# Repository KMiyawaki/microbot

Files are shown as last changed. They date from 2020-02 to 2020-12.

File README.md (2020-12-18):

# Microbot

Open source educational robot for Deep Leraning and ROS.

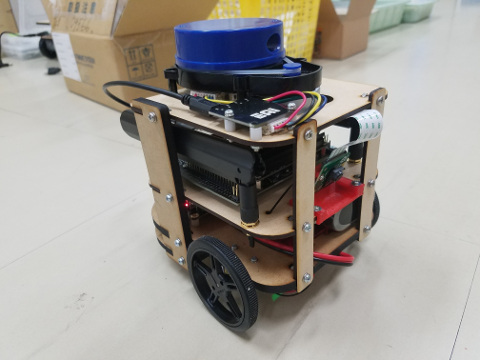
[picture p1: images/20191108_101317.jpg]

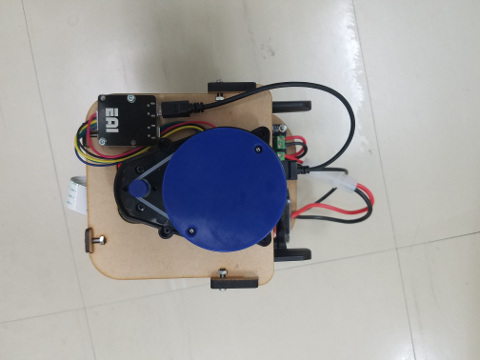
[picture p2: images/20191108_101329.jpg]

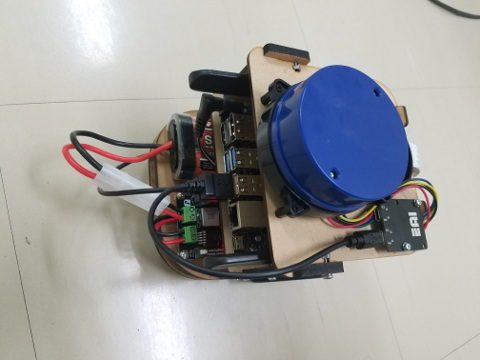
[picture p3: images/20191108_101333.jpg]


## SVG data for laser cutting

Use 5.5mm MDF board and 2.5mm MDF board

- [2.5mm](./Laser/Robot/2.5mm/All_2.5.svg)
- [5.5mm](./Laser/Robot/5.5mm/All_5.5.svg)

## Bills of materials

- [Microbot_BOM.pdf](./Microbot_BOM.pdf)

## Documents

- [Micorbot Manual](https://github.com/KMiyawaki/lectures/blob/master/ros/robots/jetson_microbot_boot_shutdown.md)
- [Jetson NANO カスタムイメージの作成](jetson_sdk.md)
- [JetCard のインストール](install_jetcard.md)
- [その他のソフトのインストール](setup_details.md)

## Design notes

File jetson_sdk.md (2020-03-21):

# NVIDIA SDK manager & docker

## Docker をインストール

- https://qiita.com/myyasuda/items/cb8e076f4dba5c41afbc
- `docker`グループに参加し、再起動する

```shell
$ sudo usermod -aG docker `whoami`
$ sudo reboot
```

- `docker ps`で以下のような出力があれば OK。

```shell
$ docker ps
CONTAINER ID        IMAGE               COMMAND             CREATED             STATUS              PORTS               NAMES
```

## 事前に大容量の領域を確保する

- ツインドライブ構成 PC の HDD に Linux 領域を作成するなど。
- `/etc/fstab`に設定を書き、マウントしておく。ここでは`/hdd`にその領域をマウントしたとして進める。
- Docker イメージの置き場所を大容量領域に変える。
  - https://qiita.com/elm200/items/43497f76cbdd19c47d8b

```shell
$ sudo systemctl stop docker.service
$ sudo mv /var/lib/docker /hdd
$ cd /etc/docker
$ sudo emacs daemon.json -nw
```

- `daemon.json`の内容は次の通り

```json
{
  "data-root": "/hdd/docker"
}
```

## Docker イメージを作成する

- `Dockerfile`をクローン

```shell
$ cd /hdd
$ git clone https://github.com/atinfinity/sdk_manager_docker.git
```

- https://developer.nvidia.com/nvidia-sdk-manager から`NVIDIA SDK Manager`バイナリをダウンロード

  - NVIDIA Developper のアカウント必要。
  - `sdkmanager_1.0.1-5538_amd64.deb` (2020/03/21 時点) このファイルを上記`sdk_manager_docker`に移動させておく。

- Docker イメージのビルド

```shell
$ cd sdk_manager_docker
$ docker build --build-arg SDK_MANAGER_VERSION=1.0.1-5538 -t jetpack .
```

- イメージの確認
  - `docker images`コマンド

```shell
$ docker images
REPOSITORY          TAG                 IMAGE ID            CREATED             SIZE
jetpack             latest              67e7931be86e        5 minutes ago       811MB
ubuntu              18.04               ccc6e87d482b        13 days ago         64.2MB
```

- Docker コンテナから X サーバーへの通信を許可する。
  - https://unskilled.site/docker%E3%82%B3%E3%83%B3%E3%83%86%E3%83%8A%E3%81%AE%E4%B8%AD%E3%81%A7gui%E3%82%A2%E3%83%97%E3%83%AA%E3%82%B1%E3%83%BC%E3%82%B7%E3%83%A7%E3%83%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
  - ホストマシン起動時に毎回必要。

```shell
$ xhost local:
non-network local connections being added to access control list
```

- ホストマシンのディレクトリを永続化領域として指定する。
  - `sdk_manager_docker/launch_container.sh`に追記してコンテナで作成したデータが消えないようにする。

```text
docker run --privileged --rm -it \
           --volume=$XSOCK:$XSOCK:rw \
           --volume=$XAUTH:$XAUTH:rw \
           --volume=/dev:/dev:rw \
           --volume=/hdd:/hdd:rw \ # 追記
```

## SDK Manager の起動

- ホストマシンのディスク容量をチェック

```shell
$ df -alh
/dev/nvme0n1p5   94G   21G   69G  24% /     # SSD 領域。ここは使わないようになっているはず。
/dev/sda2       393G  1.1G  372G   1% /hdd  # Dockerイメージを作成したHDD領域。
```

- コンテナ起動

```shell
$ cd /hdd/sdk_manager_docker
$ ./launch_container.sh
```

- コンテナ側で SDK Manager 起動

```shell
$ sdkmanager
```

- Step 1
  - Host Machine のチェックを外す。
  - Target Hardware を Jetson NANO (Developper kit version)にする。
  - Target Operating System を JetPack 4.2.2 (rev. 1) にする。
    - Jetcard のブランチ名に合わせているだけ。

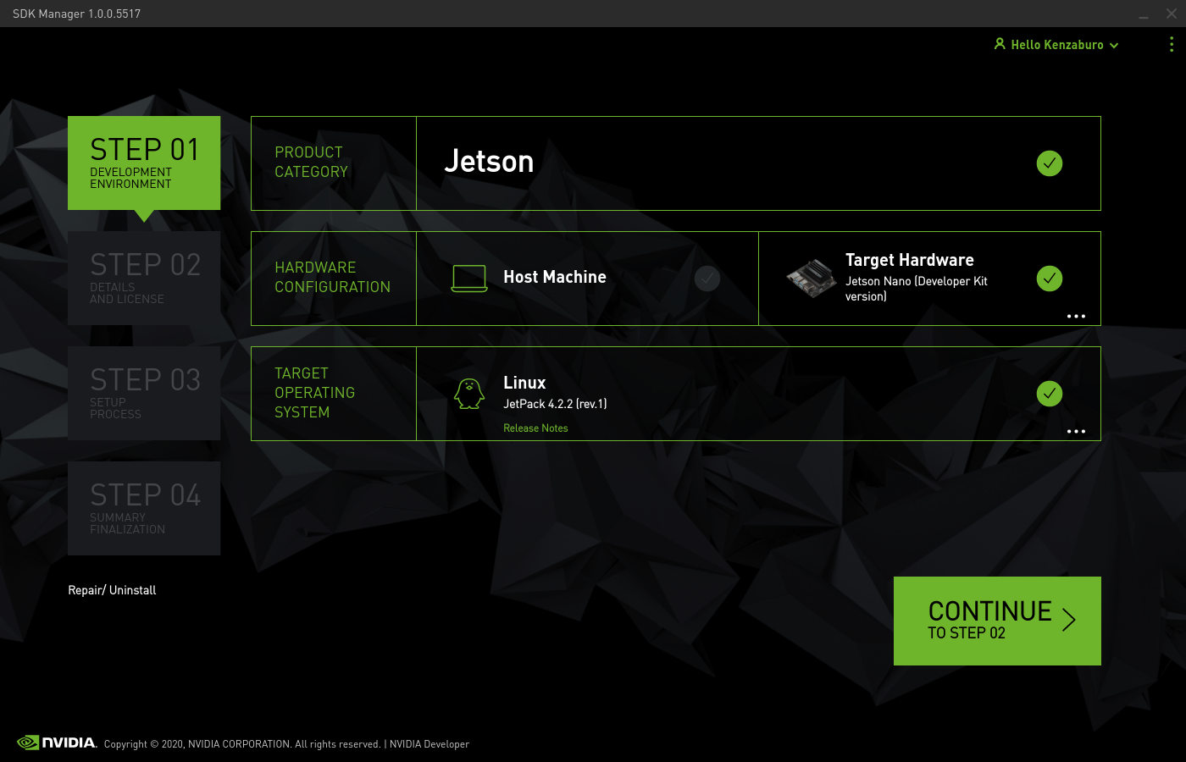
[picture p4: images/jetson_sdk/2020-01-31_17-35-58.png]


- Step 2
  - Jetson SDK Components のチェックを外す。

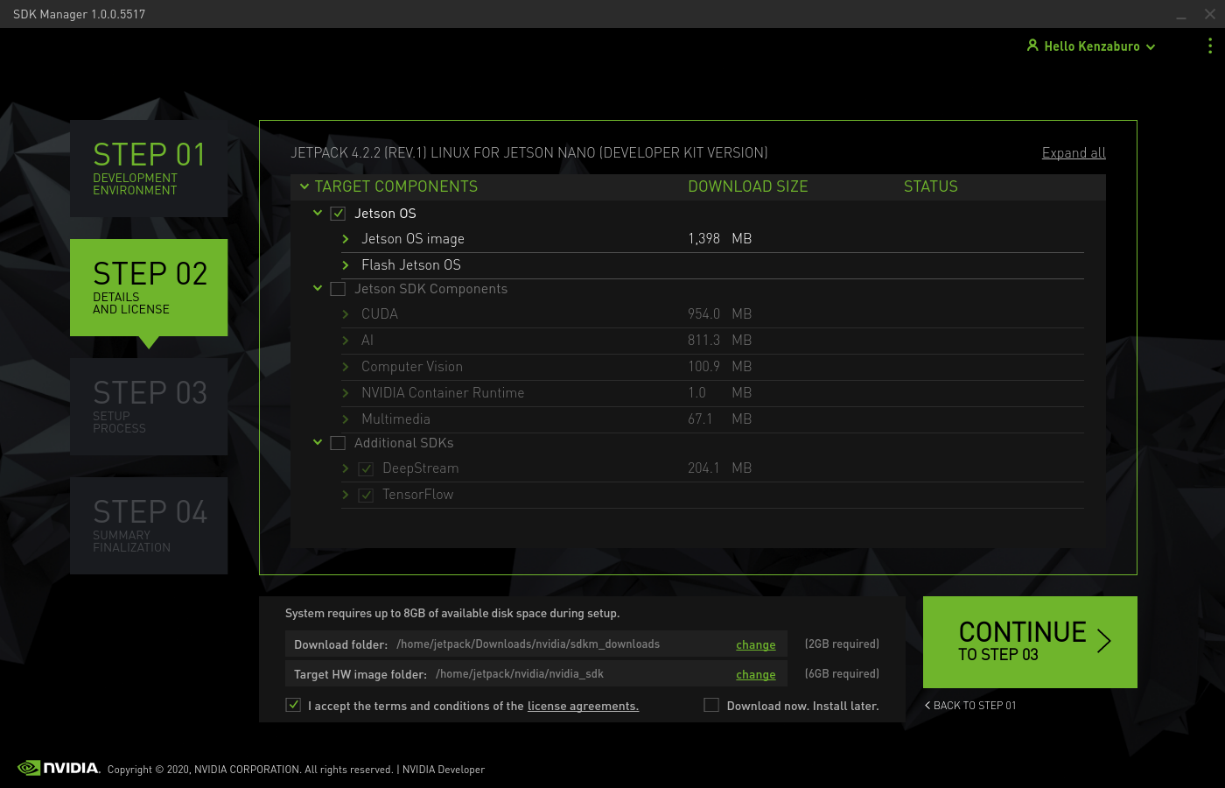
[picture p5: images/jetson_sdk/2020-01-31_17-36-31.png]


- Step 3
  - ダウンロードが始まる。

## イメージ作成に必要なファイルを抽出する

- Docker コンテナで SDK Manager によりダウンロードしたファイル群から必要なものをコピーする。

```shell
$ cd /hdd
$ mkdir nano_sd_image
$ cd nano_sd_image/
$ sudo cp -ra ~/nvidia/nvidia_sdk/JetPack_4.2.2_Linux_GA_P3448/Linux_for_Tegra/. ./
$ cp rootfs/etc/systemd/nvresizefs.sh ./
$ sudo cp rootfs/etc/systemd/system/nvresizefs.service ./
$ sudo rm -rf /hdd/nano_sd_image/rootfs/*
```

## コピーもとの Jetson NANO SD カードからデータを抽出する

- Docker 側で作成した`nano_sd_image`ディレクトリを**ホスト側**で確認する。

```shell
$ cd /hdd
$ ls
docker  nano_sd_image  sdk_manager_docker
$ cd /hdd/nano_sd_image
$ df -BG|grep media
/dev/sdb1           118G   24G       89G  22% /media/<ユーザ名>/<デバイス名>
$ sudo cp -ra /media/<ユーザ名>/<デバイス名>/. rootfs/
```

## コンテナ側でイメージを作成する

- 自動拡張スクリプトの補充

```shell
$ cd /hdd/nano_sd_image
$ sudo cp nvresizefs.sh rootfs/etc/systemd/
$ sudo cp nvresizefs.service rootfs/etc/systemd/system/
$ sudo ln -s rootfs/etc/systemd/system/nvresizefs.service rootfs/etc/systemd/system/multi-user.target.wants/nvresizefs.service
```

- sgdisk コマンドのために gdisk をインストール

```shell
$ sudo apt-get install -y gdisk
```

- イメージの作成（10 分程度）
  - `df -BG|grep media`で得られた使用済み容量より大きい値を`./create-jetson-nano-sd-card-image.sh`の引数に指定する。

```shell
$ cd /hdd/nano_sd_image
$ sudo ./create-jetson-nano-sd-card-image.sh -o backup.img -s 25G -r 200 # 25G はSDカードの使用済み容量より大きい値を設定する。
********************************************
     Jetson-Nano SD Image Creation Tool
********************************************
create-jetson-nano-sd-card-image.sh - creating backup.img of 25G...
0+0 records in
0+0 records out
0 bytes copied, 4.3765e-05 s, 0.0 kB/s
create-jetson-nano-sd-card-image.sh - creating signed images
・・・
Allocating group tables: done
Writing inode tables: done
Creating journal (32768 blocks): done
Writing superblocks and filesystem accounting information: done

********************************************
   Jetson-Nano SD Image Creation Complete
********************************************
```

- 完成したイメージを[Etcher](https://www.balena.io/etcher/)などで別の SD に焼く。

## 補足

- Docker イメージの削除
  - https://qiita.com/tifa2chan/items/e9aa408244687a63a0ae

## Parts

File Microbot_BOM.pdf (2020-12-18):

Microbot BOM | 2020/12/18
部品番号 | サムネイル | 部品構成 | 見積費用 | 数量 | ベンダー | Web リンク | 材料 | 説明
RoboClaw 2x7A | | 購入 | ¥8,657 | 1 BASIC MICRO | | https://www.basicmicro.com/Roboclaw-2x7A-Motor- Controller_p_55.html
DC-DC Power Module 25W | | 購入 | ¥1,200 | 1 DFRobot | | https://www.dfrobot.com/product-752.html
ジーフォース GE021 SMASH NiMH7.2V3800mAh [ラジ コン用バッテリー] | | 購入 | ¥3,800 | 1 GForce | | http://www.gforce-hobby.jp/products/GE020.html
(+)ナベ頭小ねじ(ステンレス) M2.6x10 | | スタンダード | ¥4 | 3 Monotaro | | https://www.monotaro.com/p/0550/7065/
(+)ナベ頭小ねじ(ステンレス) M2.6x5 | | スタンダード | ¥4 | 12 Monotaro | | https://www.monotaro.com/p/0550/7031/
(+)ナベ頭小ねじ(ステンレス) M2.6x8 | | スタンダード | ¥4 | 4 Monotaro | | https://www.monotaro.com/p/0550/7056/
(+)ナベ頭小ねじ(ステンレス) M2x8 | | スタンダード | ¥4 | 8 Monotaro | | https://www.monotaro.com/p/0550/6934/
(+)ナベ頭小ねじ(ステンレス) M3×12 | | スタンダード | ¥4 | 18 Monotaro | | https://www.monotaro.com/p/0550/7205/
スプリングワッシャー(鉄/ユニクローム) M2 | | スタンダード | ¥1 | 8 Monotaro | | https://www.monotaro.com/p/0552/9867/
スプリングワッシャー(鉄/ユニクローム) M2.6 | | スタンダード | ¥1 | 23 Monotaro | | https://www.monotaro.com/p/0552/9973/
スプリングワッシャー(鉄/ユニクローム) M3 | | スタンダード | ¥0 | 18 Monotaro | | https://www.monotaro.com/p/0552/9876/
六角ナット1種(鉄/ユニクローム) パック入 り M2 | | スタンダード | ¥2 | 8 Monotaro | | https://www.monotaro.com/p/2344/2502/

1／3

部品番号 | サムネイル | 部品構成 | 見積費用 | 数量 | ベンダー | Web リンク | 材料 | 説明
六角ナット1種(鉄/ユニクローム) パック入 り M2.6 | | スタンダード | ¥2 | 15 Monotaro | | https://www.monotaro.com/p/2344/2536/
六角ナット1種(鉄/ユニクローム) パック入 り M3 | | スタンダード | ¥1 | 18 Monotaro | | https://www.monotaro.com/p/0552/9167/
camera_mount | | スタンダード | | 1 nVidia | | https://github.com/NVIDIA-AI- IOT/jetbot/blob/master/assets/camera_mount.stl | | 3Dプリント
Jetson NANO Developper Kit | | 購入 | ¥11,400 | 1 NVidia | | https://ryoyo-gpu.jp/products/jetson/nano2/
MicrobotBottomPlate | | スタンダード | | 1 OIT | | | MDF 中密度繊維ボード | 2.5mm
MicrobotCasterPlate | | スタンダード | | 1 OIT | | | MDF 中密度繊維ボード | 5.5mm
MicrobotCasterSpacer | | スタンダード | | 1 OIT | | | MDF 中密度繊維ボード | 5.5mm
MicrobotFrontPlate | | スタンダード | | 2 OIT | | | MDF 中密度繊維ボード | 2.5mm
MicrobotMiddlePlate | | スタンダード | | 1 OIT | | | MDF 中密度繊維ボード | 2.5mm
MicrobotSidePlate | | スタンダード | | 2 OIT | | | MDF 中密度繊維ボード | 5.5mm
MicrobotTopPlate | | スタンダード | | 1 OIT | | | MDF 中密度繊維ボード | 2.5mm
100:1 金属マイクロギヤードモータ HPCB 12V 両軸仕様 | | 購入 | ¥2,133 | 2 Pololu | | https://store.shopping.yahoo.co.jp/suzakulab/pololu- 3052.html

2／3

部品番号 | サムネイル | 部品構成 | 見積費用 | 数量 | ベンダー | Web リンク | 材料 | 説明
ホイール 60×8mm ブラック 2個入り | | 購入 | ¥479 | 1 Pololu | | https://store.shopping.yahoo.co.jp/suzakulab/Pololu- 1420.html
金属マイクロギヤードモータ 拡張ブラ ケット 2個入り | | 購入 | ¥562 | 1 Pololu | | https://store.shopping.yahoo.co.jp/suzakulab/pololu- 1089.html
ＲａｓｐｂｅｒｒｙＰｉカメラモジュール Ｖ２ | | 購入 | ¥4,300 | 1 RSコンポーネンツ株式会社 | | https://jp.rs-online.com/web/p/video- modules/9132664/
YDLidar X4 | | 購入 | ¥12,100 | 1 Shenzhen EAI Technology Co., Ltd | | https://www.switch-science.com/catalog/5412/
面打ボールキャスター BM-15 | | 購入 | ¥560 | 1 スガツネ工業 | | http://search.sugatsune.co.jp/product/g/gBM/
SJA-2606 | | スタンダード | ¥18 | 4 テイシン | | https://www.monotaro.com/p/0990/7162/ | | 六角両雌ねじスペーサー
SJB-2606 | | 購入 | ¥30 | 8 テイシン | | https://www.monotaro.com/p/0990/8422/
LP-02-1 【タミヤコネクタ】6.2mmピッチ 中継用L コネクタ プラグハウジング | | | | | 日本圧着端子製造 (JST) | https://www.sengoku.co.jp/mod/sgk_cart/detail.php?c ode=EEHD-4KC7

リード線

Pololu 金属マイクロギヤードモータ用磁気 エンコーダキット 12CPR 2.7V-18V (HPCB対応) 2個入り | | | 1108 | 1 | | https://store.shopping.yahoo.co.jp/suzakulab/Pololu- 3081.html | | 半田付けが非常に難しいので、販売元に有料委託する か、後継機種 （https://store.shopping.yahoo.co.jp/suzakulab/Pololu-4760.html）の利用を推奨（動作未確認）。

3／3

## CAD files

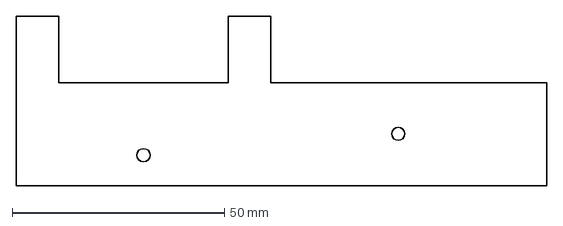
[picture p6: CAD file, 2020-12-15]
Laser/Base/Side.dxf
125.0 x 40.0 mm

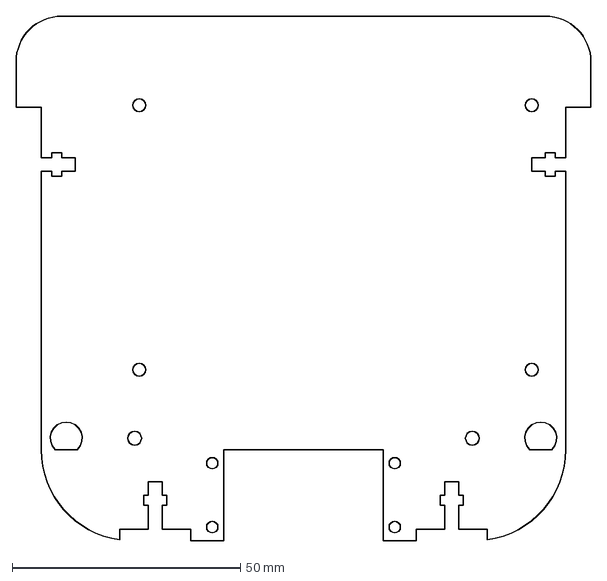
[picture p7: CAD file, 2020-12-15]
Laser/Robot/2.5mm/Middle.dxf
126.0 x 115.0 mm

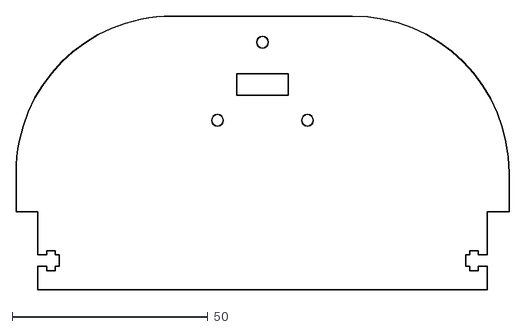
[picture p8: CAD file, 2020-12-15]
Laser/Robot/5.5mm/CasterBase.dxf
126.0 x 70.0

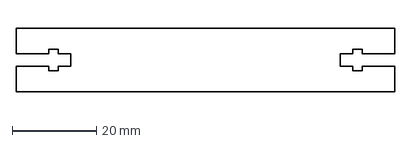
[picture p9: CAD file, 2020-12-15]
Laser/Base/BasePlate.dxf
90.0 x 15.0 mm

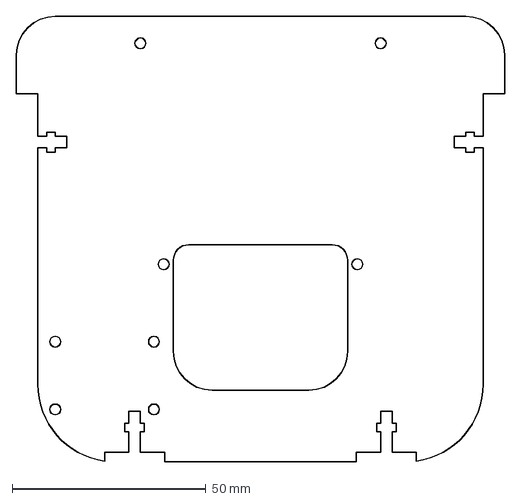
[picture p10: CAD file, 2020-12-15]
Laser/Robot/2.5mm/Top.dxf
126.0 x 115.0 mm

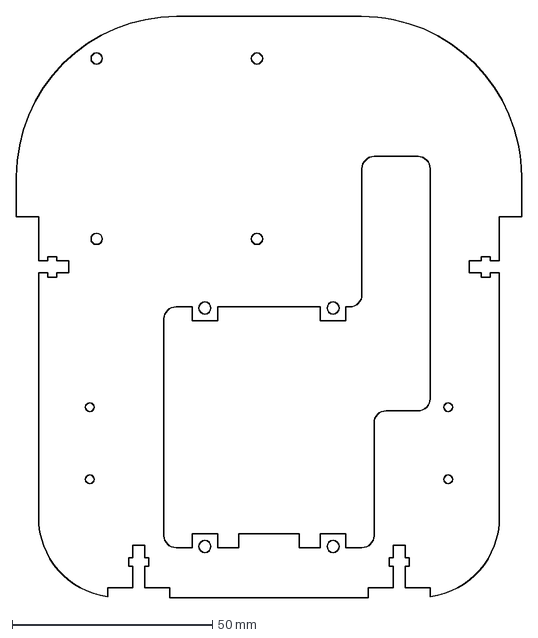
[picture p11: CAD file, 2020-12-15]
Laser/Robot/5.5mm/Bottom.dxf
126.0 x 145.0 mm

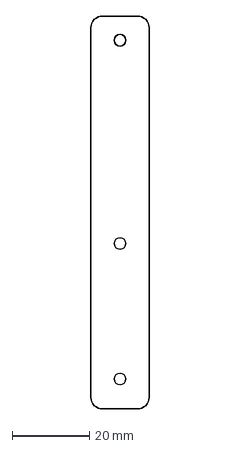
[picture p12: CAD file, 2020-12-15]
Laser/Robot/2.5mm/Front.dxf
15.0 x 101.5 mm

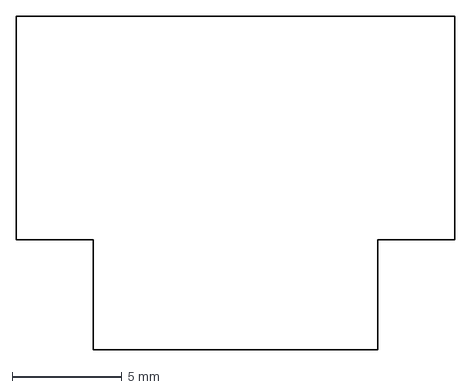
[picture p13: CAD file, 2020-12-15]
Laser/Robot/5.5mm/CasterSpacer.dxf
20.0 x 15.2 mm

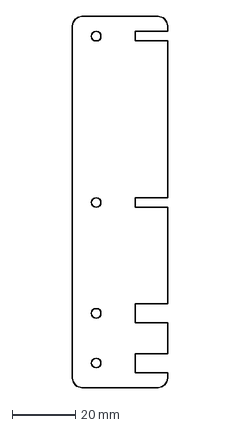
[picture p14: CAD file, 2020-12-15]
Laser/Robot/5.5mm/Side.dxf
30.0 x 117.2 mm

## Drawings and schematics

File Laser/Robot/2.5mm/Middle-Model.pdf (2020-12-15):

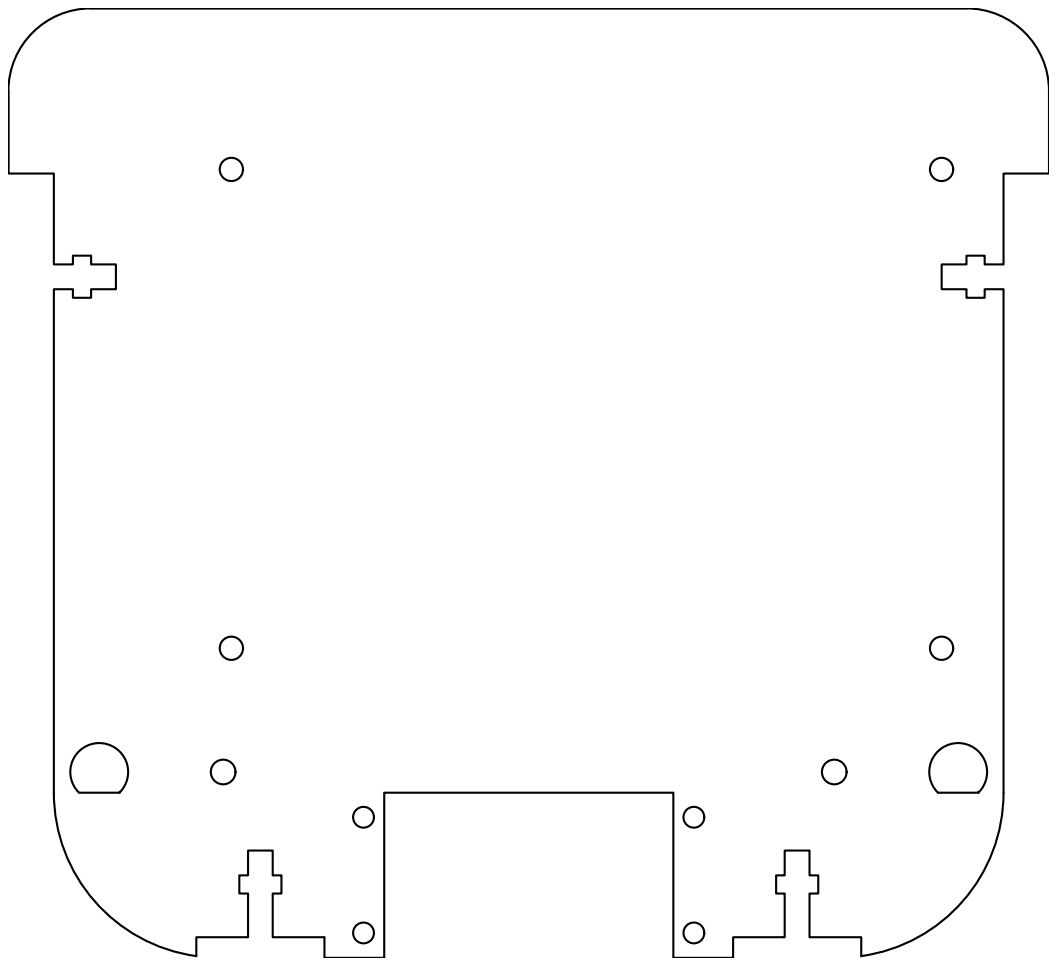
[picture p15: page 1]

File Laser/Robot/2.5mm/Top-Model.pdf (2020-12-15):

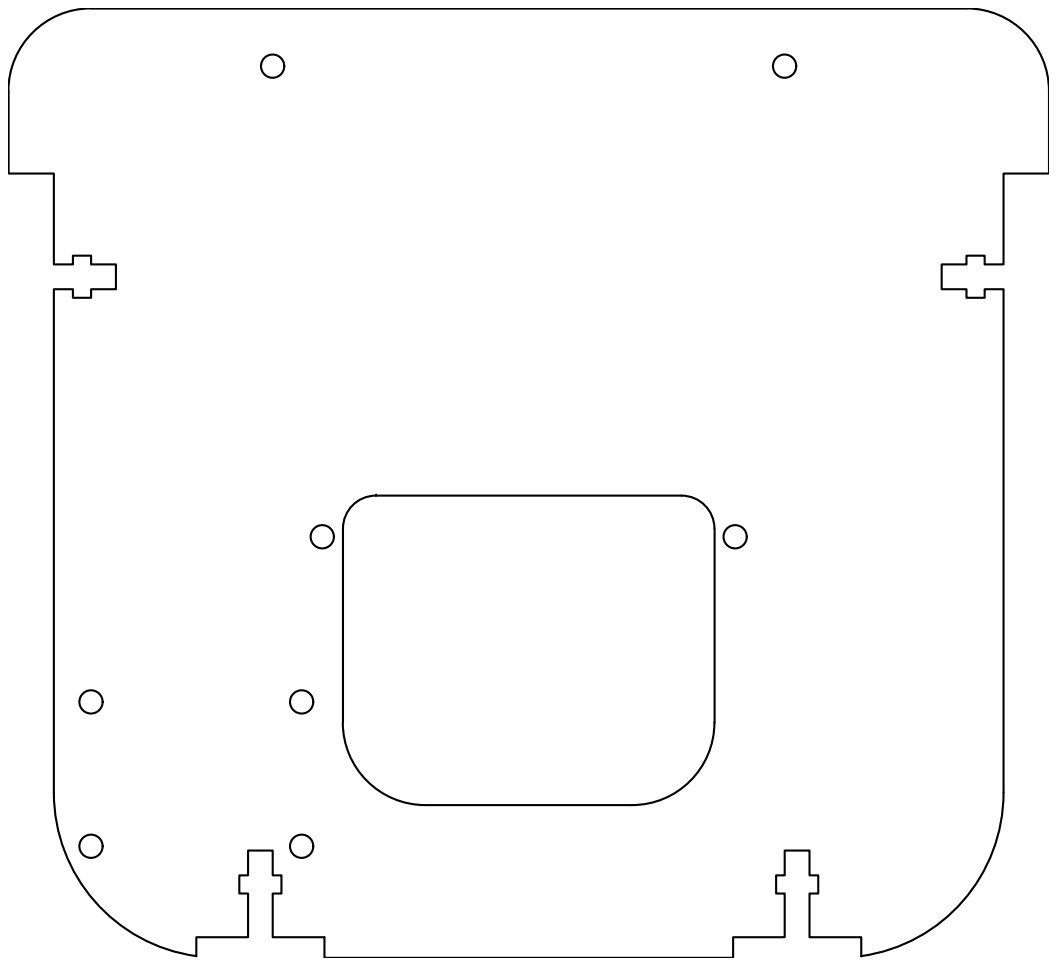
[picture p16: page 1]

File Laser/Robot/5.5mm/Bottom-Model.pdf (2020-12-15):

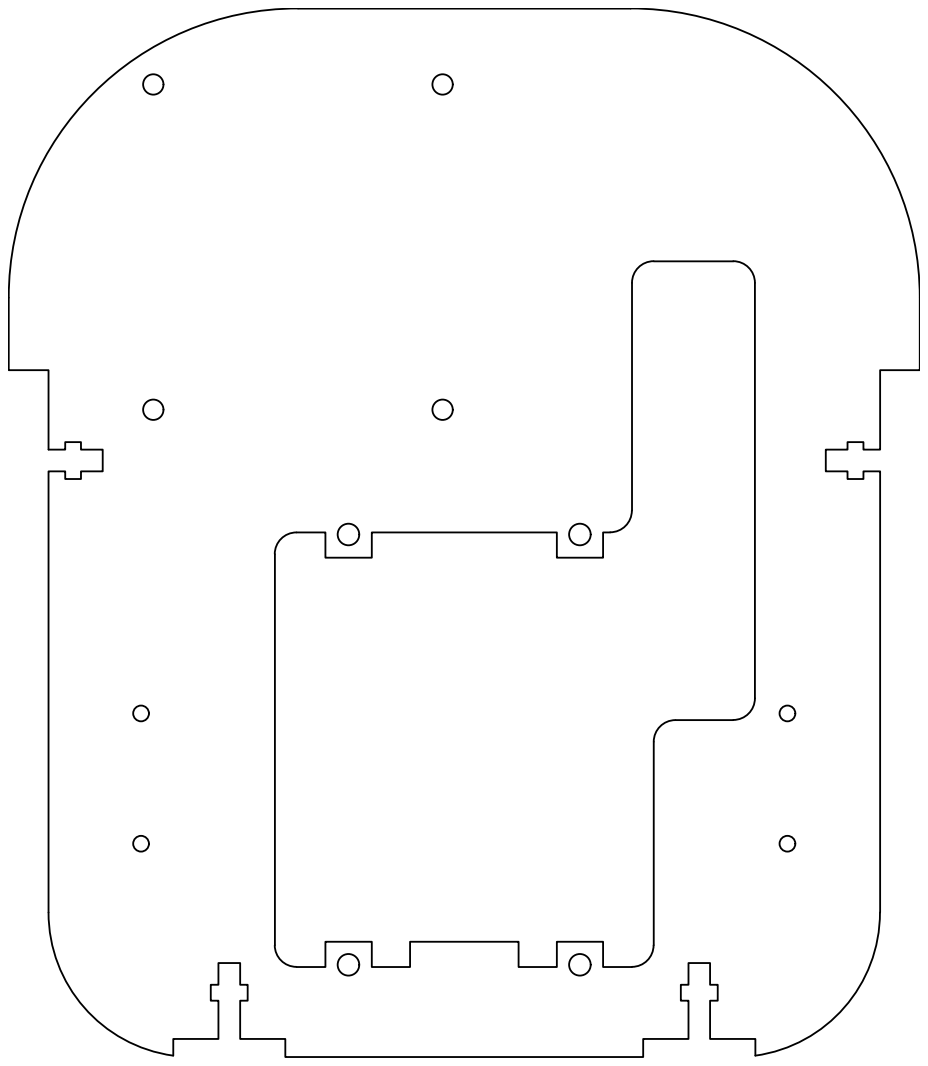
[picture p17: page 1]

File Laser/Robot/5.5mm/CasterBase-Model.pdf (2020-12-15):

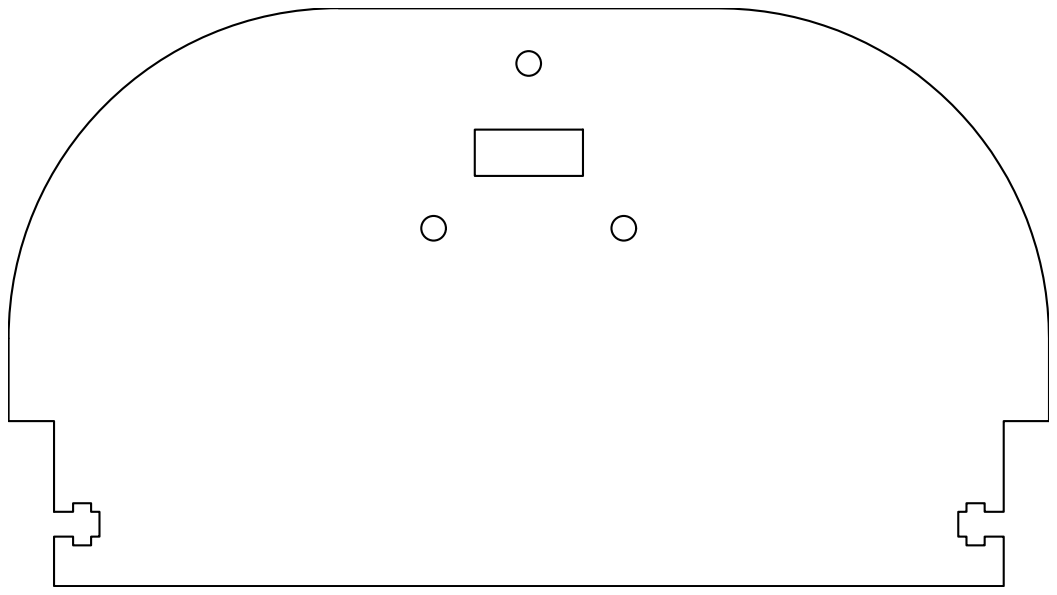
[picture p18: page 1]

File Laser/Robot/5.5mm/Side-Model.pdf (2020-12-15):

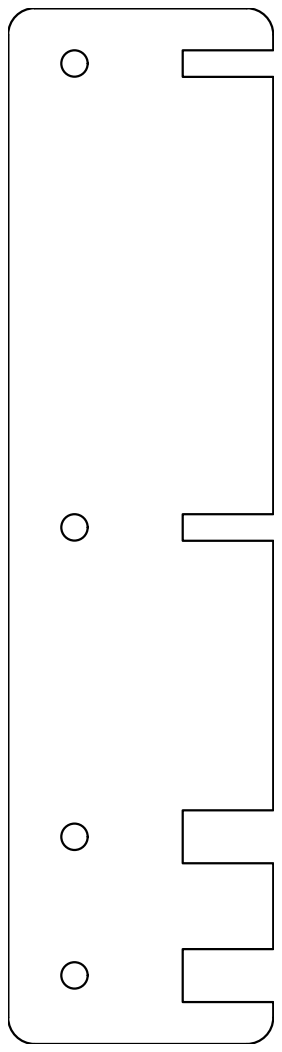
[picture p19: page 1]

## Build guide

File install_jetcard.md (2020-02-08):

# JetCard のインストール

- JetCard のリポジトリ
  - https://github.com/NVIDIA-AI-IOT/jetcard/tree/jetpack_4.2.2

## Jetson NANO のイメージ書き込み

- Jetson NANO の SD カードイメージは一応、 branch と合わせ、Jetpack 4.2.2 からダウンロードする。
  - https://developer.nvidia.com/embedded/jetpack
  - ファイル名は`nv-jetson-nano-sd-card-image-r32.2.1.zip`
- ユーザ名は`jetson`でないと下記エラーが出る。パスワードは任意と思われるが、`jetson`としておく。

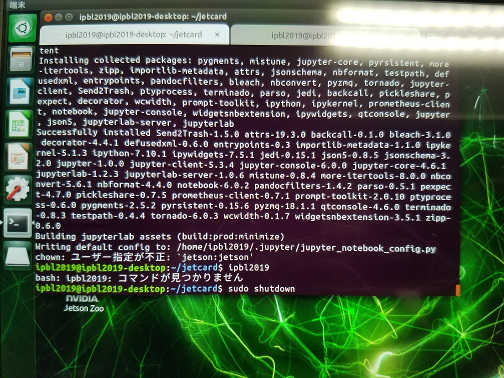
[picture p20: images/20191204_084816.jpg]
ユーザ名不正


- ネットワーク接続後、下記を先に実行しておく。
  - https://github.com/NVIDIA-AI-IOT/jetcard/blob/jetpack_4.2.2/install.sh#L12
  - https://github.com/NVIDIA-AI-IOT/jetcard/blob/jetpack_4.2.2/install.sh#L54

```shell
sudo apt-get update
sudo apt install -y python3-pip python3-pil python3-smbus python3-matplotlib cmake
cd
git clone https://github.com/NVIDIA-AI-IOT/jetcard.git
cd jetcard
git checkout -b jetpack_4.2.2 origin/jetpack_4.2.2
sudo python3 setup.py install
```

## JetCard インストール時のポイント

- 後は https://github.com/NVIDIA-AI-IOT/jetcard/tree/jetpack_4.2.2 に従って、`install.sh`を実行すればよい。
  - おおよそ３，４時間程度。
- 上記で`sudo python3 setup.py install`をしていないと、次のエラーが出る可能性がある。

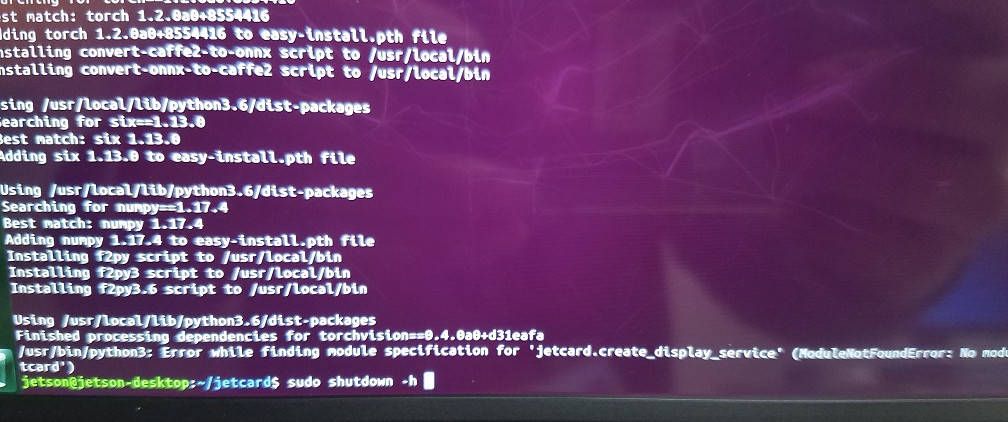
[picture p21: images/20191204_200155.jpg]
jetcard.create_display_service.py


- インストール中に下記エラーが出るが、問題はない。
  - [missing files: ['..../plugin.js'] error #1](https://github.com/jaybdub/jupyter_clickable_image_widget/issues/1)

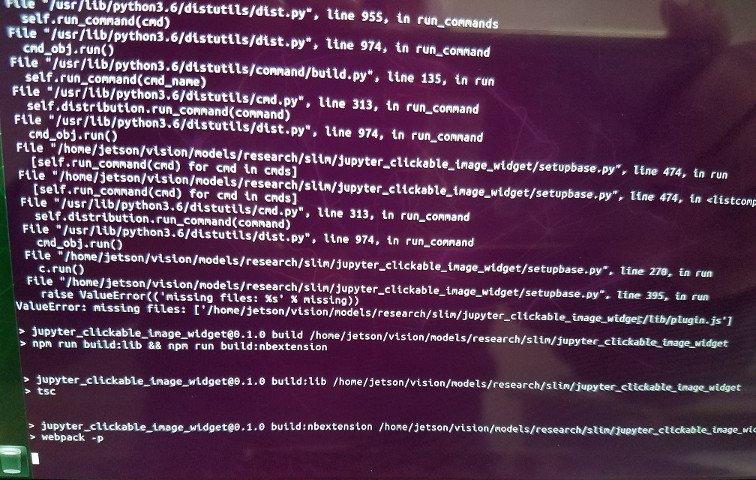
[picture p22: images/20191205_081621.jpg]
jypiter_clickable_image_widget


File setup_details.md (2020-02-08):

# ソフトのセットアップ

## Jetson NANO

- イメージを SD カードに焼き付けて、日本語設定その他を済ませる。

```shell
sudo apt update ;sudo apt dist-upgrade -y;sudo apt autoremove -y
sudo apt install emacs
```

### VSCode

- [参考](https://qiita.com/koppe/items/64d155bc7814441920f9)

```shell
curl -L https://github.com/toolboc/vscode/releases/download/1.32.3/code-oss_1.32.3-arm64.deb -o code-oss_1.32.3-arm64.deb
sudo dpkg -i code-oss_1.32.3-arm64.deb
```

### Chrome のログインキーリングを解除

- [参考](https://www.petitmonte.com/linux/chrome_login_keyring.html)

### pip

```shell
sudo apt install python-pip
```

## ROS

- [Ubuntu install of ROS Melodic](http://wiki.ros.org/melodic/Installation/Ubuntu)に従って、ROS をインストール。
  - `ros-melodic-desktop-full`

```shell
sudo apt install ros-melodic-rosemacs
emacs -nw ~/.emacs.d/init.el
```

- 以下を貼り付け。

```text
(setq inhibit-startup-message t)
(add-to-list 'load-path "/opt/ros/melodic/share/emacs/site-lisp")
;; or whatever your install space is + "/share/emacs/site-lisp"
(require 'rosemacs-config)
```

- ROS のワークスペース作成

```shell
mkdir -p ~/catkin_ws/src
cd ~/catkin_ws/src/
catkin_init_workspace
cd ..
catkin_make
cd
emacs .bashrc &
```

- 末尾に下記を追記。

```text
source ~/catkin_ws/devel/setup.bash
```

- 必要なパッケージのインストール

```shell
sudo apt install ros-melodic-navigation
sudo apt install ros-melodic-joy
sudo apt install ros-melodic-teleop-twist-joy
sudo apt install ros-melodic-laser-filters
sudo apt install ros-melodic-slam-gmapping
```

- ユーザをグループ dialout に追加

```shell
sudo gpasswd -a $(whoami) dialout
```

- 一旦ログアウト

- pycrc のインストール

```shell
sudo pip install pycrc
```

- microbot 用ソフトをクローン

```shell
cd ~/catkin_ws/src
git clone https://github.com/KMiyawaki/oit_navigation_microbot_01.git
git clone https://github.com/KMiyawaki/oit_roboclaw_driver.git
git clone https://github.com/KMiyawaki/my_microbot_apps.git
```

- YDLidar 用ソフトをクローン

```shell
cd ~/catkin_ws/src
git clone https://github.com/YDLIDAR/ydlidar_ros.git
```

- ビルド

```shell
cd ~/catkin_ws
catkin_make
```

- YDLidar 用 udev

```shell
roscd ydlidar_ros/startup/
sudo sh initenv.sh
```

- 一旦再起動

## Wifi アクセスポイント化

- [参考](https://qiita.com/ishihatta/items/c95308265af0c2ddfea1)
- GUI で行えば良い。
- セキュリティも不要。

## Deep learning 関連

- darknet_ros(不要？)

  - [参考](https://github.com/leggedrobotics/darknet_ros)

- jetbot のソフトをインストール

```shell
cd ~
git clone https://github.com/dusty-nv/jetson-inference
cd jetson-inference
git submodule update --init
mkdir build
cd build
cmake ../
make
```

- 途中どのモデルをダウンロードするかが出てくる。とりあえず、デフォルトで。
- pyTorch のどのバージョンをインストールするか聞いてくる。とりあえず、Python2.7 と Python3.6 両方をインストール。

```shell
sudo make install

sudo apt-get install ros-melodic-vision-msgs ros-melodic-image-transport ros-melodic-image-publisher
cd ~/catkin_ws/src
git clone https://github.com/dusty-nv/ros_deep_learning
cd ~/catkin_ws
catkin_make

cd ~/catkin_ws/src
git clone https://github.com/dusty-nv/jetbot_ros

# build the package
cd ~/catkin_ws
catkin_make
```

## SainSmart IMX219 カメラ モジュール

- カメラから得られる画像にピンク色がかかっているのを修正する。
- [Jetson NANO フォーラムの記事](https://devtalk.nvidia.com/default/topic/1051913/jetson-nano/how-to-close-gstreamer-pipeline-in-python/post/5340291/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)
- ファイルを[ダウンロード](https://www.dropbox.com/s/ougz816496m4ilw/camera_overrides.isp?dl=0)
- `/var/nvidia/nvcam/settings/camera_overrides.isp`として配置し、下記コマンドを実行。

```shell
sudo chmod 664 /var/nvidia/nvcam/settings/camera_overrides.isp
sudo chown root:root /var/nvidia/nvcam/settings/camera_overrides.isp
```

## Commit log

2020-12-15 add: SVG data
    [BasePlate.dxf, Bottom.dxf, CasterBase.dxf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]
2020-12-15 add: BOM
    [201215_MicrobotBOM.xlsx]
2020-12-18 modify: BOM
    [201215_MicrobotBOM.xlsx, Microbot_BOM.xlsx]
2020-12-18 add: Encoder Kit
    [Microbot_BOM.xlsx]
